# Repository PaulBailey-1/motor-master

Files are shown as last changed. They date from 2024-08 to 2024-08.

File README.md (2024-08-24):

# MotorMaster
This is a board designed to easily command FRC motors for testing or prototyping. It currently supports motors with the Talon FX motor controller. This repo contains the board schematics, PCB layout, and firmware for the board. 

## Features
It features 2 PWM channels that can be connected directly to the CAN connectors of the motor to command a duty cycle. Pressing the test button will output a 50% duty cycle on both PWM channels.  

The board can also be connected to motors through the CAN bus. Connect one end of the CAN chain to the CAN connector on the board and the other end to the TERM connector, or use another termination resistor. 
NOTE: CAN functionality is still experimental and may not work, feel free to work on it.

The e-stop button will prevent the board from outputting any commands until the MCU is reset with the reset button. 

The EXT pins can be used to connect an external input, like a switch or button, to provide additional control such as driving a motor or as an e-stop. The functionality must be added to the code, by default it does nothing.

The board can be powered through the USB C port, or from the power terminal off of a 12V battery. The board does not supply the motor with power, but it is important that it shares ground with the motor. 

The board is designed to be used over Bluetooth with its accompanying app, the source of which is here: https://github.com/PaulBailey-1/motor-master-app  
It is a cross-platform app and so should be able to be compiled for Android and iOS, but it has only been tested for Android. 

## Manufacturing
Board gerbers exported for manufacture by OSHPark are included in the repo, otherwise, the board can be opened in KiCad to export for manufacture. The BOM can be ordered from either Mouser or DigiKey.  

The FTDI header (J5) and the EXT header (J6) are optional. The USBC TVS diode (D2) may also be omitted since it is hard to solder without bridges, although it does make the USB lines vulnerable to damage from ESD. The USB C may also be omitted entirely (J1 & D2), and the board can be programmed through the FTDI header. 

To assemble the board, a stencil can be ordered and used to apply solder paste to the pads. The solder then may be reflowed in an oven or with hot air. It may also be possible to have it assembled by the PCB fab house.

## Programming
Dependencies:
* CAN by Sandeep Mistry v0.3.1
* ESP32Servo by Kevin Harrington & John K. Bennett v3.0.5

To program the board, connect to it with USB C or with an FTID adapter and program it with the Arduino IDE. Install the ESP32 boards and the required libraries, select 'ESP32S3 Dev Module' as the board, and upload.  

The name of the board over Bluetooth can have a postfix added to it in the code to help distinguish it.
The first time the board is programmed after being assembled, the Boot button must be held from when it is plugged until it has been flashed.
For debugging over USB C make sure the 'USB CDC On Boot' option is enabled so that you can get logging over the serial port.

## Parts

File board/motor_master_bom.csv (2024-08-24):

Reference | Value | Qty | Mfr_Number | Supplier | Supplier_Number
C1,C2,C4,C10 | 10uF | 4 | C0603C106M9PAC | Mouser | 80-C0603C106M9PAC
C3,C5,C6,C7,C8,C9,C11,C14 | 0.1uF | 8 | C0603C104K5RAC3121 | Mouser | 80-C603C104K5RAC3121
C12,C13 | 100p | 2 | C0603C101J1GAC7411 | Mouser | 80-C0603C101J1GACLR
C15 | 4.7n | 1 | C0603C472J5GACTU | Mouser | 80-C0603C472J5G
D1,D4 | SK14 | 2 | SK14 | Mouser | 637-SK14
D2 | TPD4E02B04DQAR | 1 | TPD4E02B04DQAR | Mouser | 595-TPD4E02B04DQAR
D3 | 150060RS75000 | 1 | 150060RS75000 | Mouser | 710-150060RS75000
D5 | 150060RS75000 | 1 | 150060VS75000 | Mouser | 710-150060VS75000
D6 | SZNUP2105LT1G | 1 | SZNUP2105LT1G | Mouser | 863-SZNUP2105LT1G
IC1 | LM1117MPX-3.3_NOPB | 1 | LM1117MPX-3.3/NOPB | Mouser | 926-LM1117MPX3.3NOPB
IC2 | SN65HVD232DR | 1 | SN65HVD232DR | Mouser | 595-SN65HVD232DR
J1 | USB4105-GF-A | 1 | USB4105-GF-A-120 | Mouser | 640-USB4105-GF-A-120
J2 | 5-12V | 1 | 1190297 | Mouser | 651-1190297
J3,J4,J7,J8 | -- mixed values -- | 4 | 705430002 | Mouser | 538-70543-0002
J5 | FTDI | 1 | M20-9990446 | Mouser | 855-M20-9990446
J6 | EXT | 1 | TSW-102-07-T-S | Mouser | 200-TSW10207TS
R1,R2 | 5.1k | 2 | CRCW06035K10FKEA | Mouser | 71-CRCW0603-5.1K-E3
R3,R9 | 100 | 2 | CRCW0603100RFKEA | Mouser | 71-CRCW0603-100-E3
R4,R5,R6,R7,R8 | 10k | 5 | CRCW060310K0FKEA | Mouser | 71-CRCW0603-10K-E3
R10,R11 | 60 | 2 | CRCW120660R0KNAIF | Mouser | 71-CRCW120660R0KNAIF
R12 | 120 | 1 | CRCW0603120RFKEA | Mouser | 71-CRCW0603-120-E3
S1,S2,S3 | -- mixed values -- | 3 | PTS636 SKG25J SMTR LFS | Mouser | 611-PTS636SKG25JSMTR
S4 | E-Stop | 1 | FSM4JH | Mouser | 506-FSM4JH
U1 | ESP32-S3-WROOM-1-N8 | 1 | ESP32-S3-WROOM-1-N8 | Mouser | 356-ESP32-S3WROOM1N8

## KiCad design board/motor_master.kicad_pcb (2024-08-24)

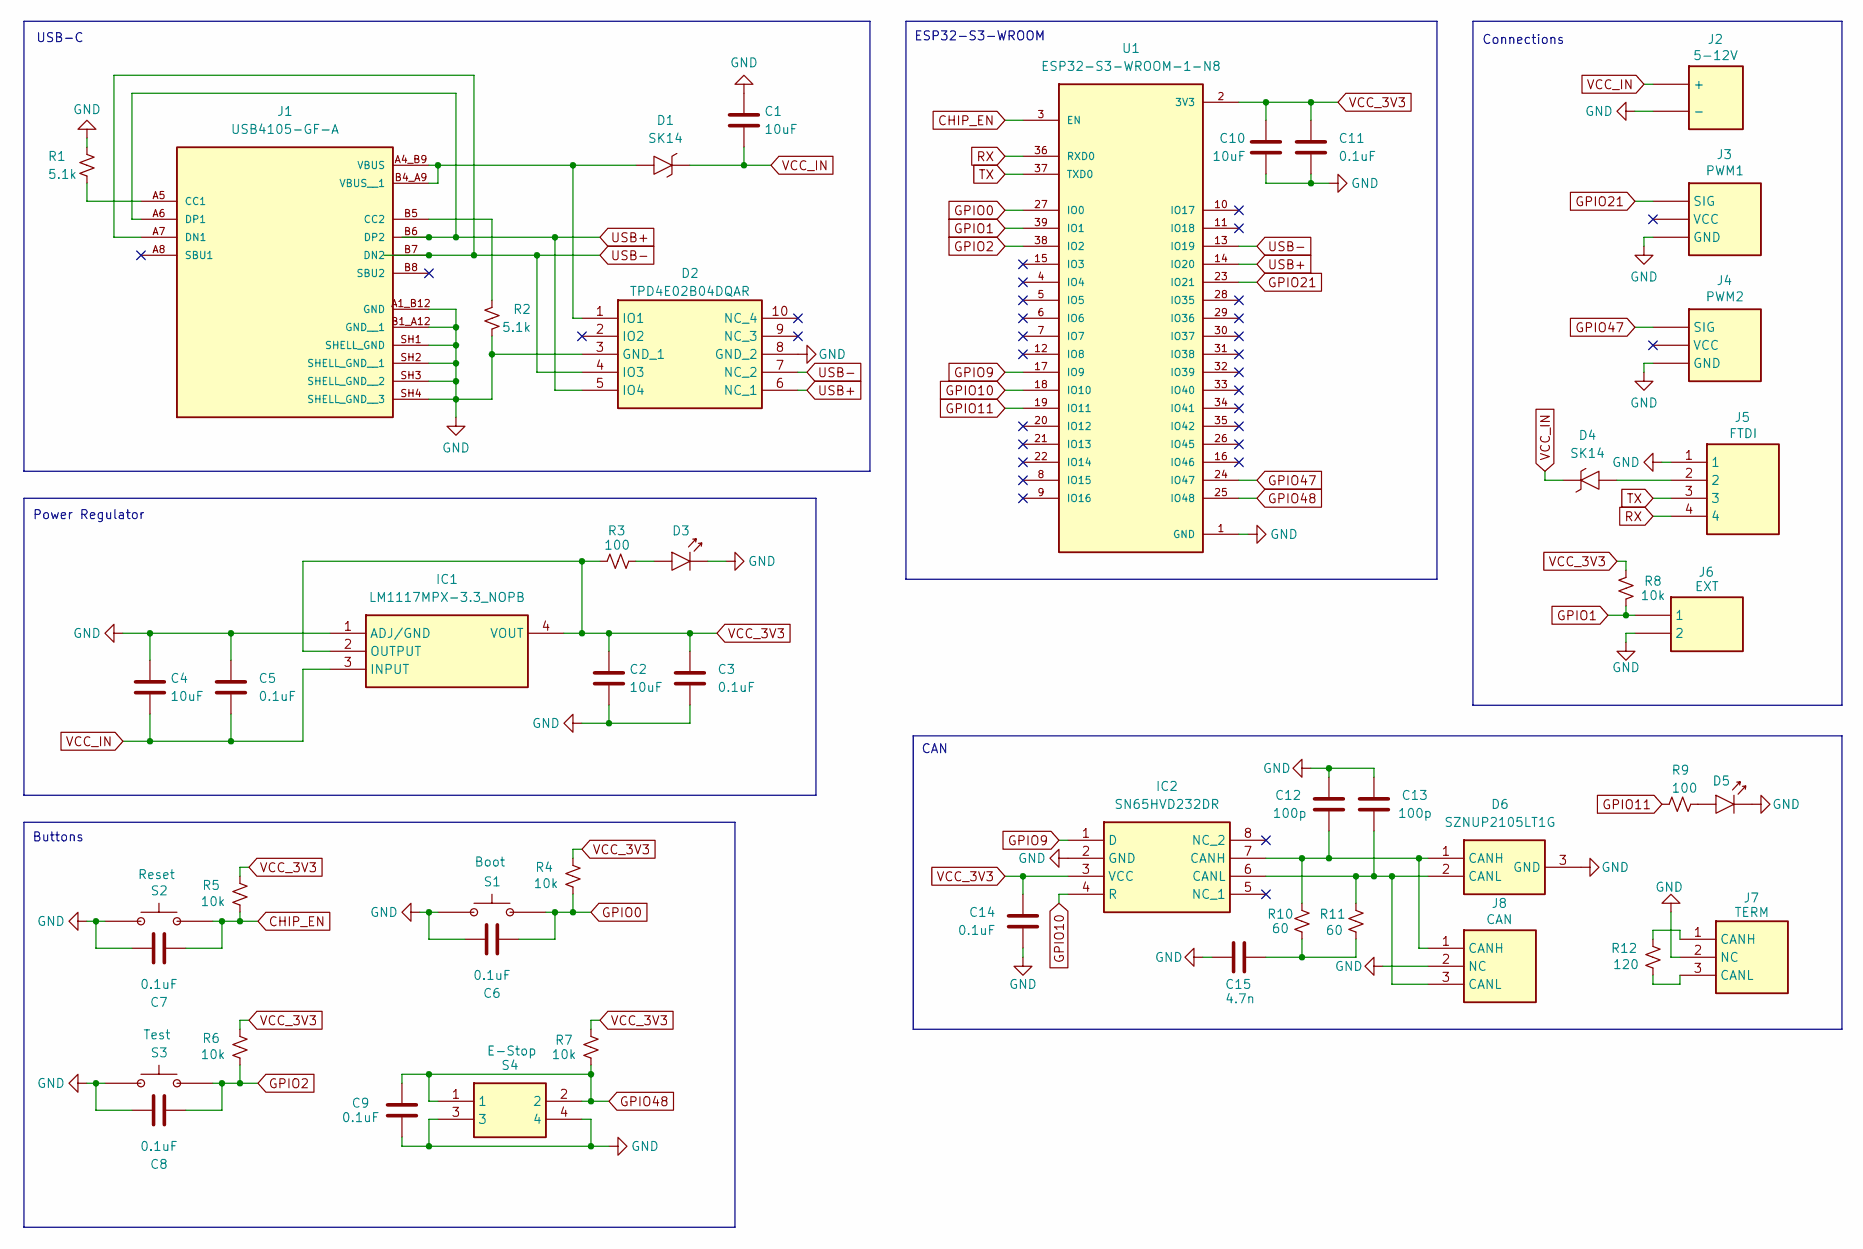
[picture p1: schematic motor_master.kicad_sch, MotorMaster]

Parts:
C1, C2, C4, C10: 10uF; C_0603_1608Metric
C3, C5, C6, C7, C8, C9, C11, C14: 0.1uF; C_0603_1608Metric
C12, C13: 100p; C_0603_1608Metric
C15: 4.7n; C_0603_1608Metric
D1, D4: SK14; DIONM5027X250N; Mouser Part Number 637-SK14
D2: TPD4E02B04DQAR; DQA_R-PUSON-N10_; Mouser Part Number 595-TPD4E02B04DQAR
D3, D5: 150060RS75000; LEDC1608X80N; Mouser Part Number 710-150060RS75000
D6: SZNUP2105LT1G; SOT96P237X111-3N; Mouser Part Number 863-SZNUP2105LT1G
IC1: LM1117MPX-3.3_NOPB; SOT230P700X180-4N; Mouser Part Number 926-LM1117MPX3.3NOPB
IC2: SN65HVD232DR; SOIC127P600X175-8N; Mouser Part Number 595-SN65HVD232DR
J1: USB4105-GF-A; GCT_USB4105-GF-A; PARTREV B3
J2: 5-12V; 1190297; Mouser Part Number 651-1190297
J3: PWM1; 1719710103; Mouser Part Number 200-TSW10307TS
J4: PWM2; 1719710103; Mouser Part Number 200-TSW10307TS
J5: FTDI; HDRV4W64P0X254_1X4_1016X254X889P; Mouser Part Number 855-M20-9990446
J6: EXT; TSW-102-XX-YY-S; Mouser Part Number 200-TSW10207TS
J7: TERM; 1719710103; Mouser Part Number 200-SSW10301FS
J8: CAN; 1719710103; Mouser Part Number 200-TSW10307TS
R1, R2: 5.1k; R_0603_1608Metric
R3, R9: 100; R_0603_1608Metric
R4, R5, R6, R7, R8: 10k; R_0603_1608Metric
R10, R11: 60; R_1206_3216Metric
R12: 120; R_0603_1608Metric
S1: Boot; PTS636SKG25JSMTRLFS; Mouser Part Number 611-PTS636SKG25JSMTR
S2: Reset; PTS636SKG25JSMTRLFS; Mouser Part Number 611-PTS636SKG25JSMTR
S3: Test; PTS636SKG25JSMTRLFS; Mouser Part Number 611-PTS636SKG25JSMTR
S4: E-Stop; FSM4JH; Mouser Part Number 506-FSM4JH
U1: ESP32-S3-WROOM-1-N8; XCVR_ESP32-S3-WROOM-1-N8

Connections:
CHIP_EN: C7.2, R5.1, S2.2 (NO), U1.3 (EN)
GND: C1.1, C2.2, C3.2, C4.1, C5.1, C6.1, C7.1, C8.1, C9.2, C10.2, C11.2, C12.2, C13.2, C14.1, C15.1, D2.3 (GND_1), D2.8 (GND_2), D3.2 (A), D5.2 (A), D6.3 (GND), IC1.1 (ADJ/GND), IC2.2 (GND), J1.A1_B12 (GND), J1.B1_A12 (GND__1), J1.SH1 (SHELL_GND), J1.SH2 (SHELL_GND__1), J1.SH3 (SHELL_GND__2), J1.SH4 (SHELL_GND__3), J2.3 (-), J2.4 (-), J3.3 (GND), J4.3 (GND), J5.1, J6.2, J7.2 (NC), J8.2 (NC), R1.1, R2.2, S1.1 (COM), S2.1 (COM), S3.1 (COM), S4.3, S4.4, U1.1 (GND), U1.40 (GND), U1.41_1 (GND), U1.41_2 (GND), U1.41_3 (GND), U1.41_4 (GND), U1.41_5 (GND), U1.41_6 (GND), U1.41_7 (GND), U1.41_8 (GND), U1.41_9 (GND)
GPIO0: C6.2, R4.1, S1.2 (NO), U1.27 (IO0)
GPIO1: J6.1, R8.1, U1.39 (IO1)
GPIO2: C8.2, R6.1, S3.2 (NO), U1.38 (IO2)
GPIO9: IC2.1 (D), U1.17 (IO9)
GPIO10: IC2.4 (R), U1.18 (IO10)
GPIO11: R9.2, U1.19 (IO11)
GPIO21: J3.1 (SIG), U1.23 (IO21)
GPIO47: J4.1 (SIG), U1.24 (IO47)
GPIO48: C9.1, R7.1, S4.1, S4.2, U1.25 (IO48)
unnamed: C15.2, R10.1, R11.1
unnamed: D1.2 (A), D2.1 (IO1), J1.A4_B9 (VBUS), J1.B4_A9 (VBUS__1)
unnamed: D3.1 (K), R3.1
unnamed: D4.2 (A), J5.2
unnamed: D5.1 (K), R9.1
unnamed: C12.1, D6.1 (CANH), IC2.7 (CANH), J8.1 (CANH), R10.2
unnamed: C13.1, D6.2 (CANL), IC2.6 (CANL), J8.3 (CANL), R11.2
unnamed: J1.A5 (CC1), R1.2
unnamed: J1.B5 (CC2), R2.1
unnamed: J7.1 (CANH), R12.2
unnamed: J7.3 (CANL), R12.1
RX: J5.4, U1.36 (RXD0)
TX: J5.3, U1.37 (TXD0)
USB+: D2.5 (IO4), D2.6 (NC_1), J1.A6 (DP1), J1.B6 (DP2), U1.14 (IO20)
USB-: D2.4 (IO3), D2.7 (NC_2), J1.A7 (DN1), J1.B7 (DN2), U1.13 (IO19)
VCC_3V3: C2.1, C3.1, C10.1, C11.1, C14.2, IC1.2 (OUTPUT), IC1.4 (VOUT), IC2.3 (VCC), R3.2, R4.2, R5.2, R6.2, R7.2, R8.2, U1.2 (3V3)
VCC_IN: C1.2, C4.2, C5.2, D1.1 (K), D4.1 (K), IC1.3 (INPUT), J2.1 (+), J2.2 (+)

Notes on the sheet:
USB-C
Connections
ESP32-S3-WROOM
CAN
Power Regulator
Buttons

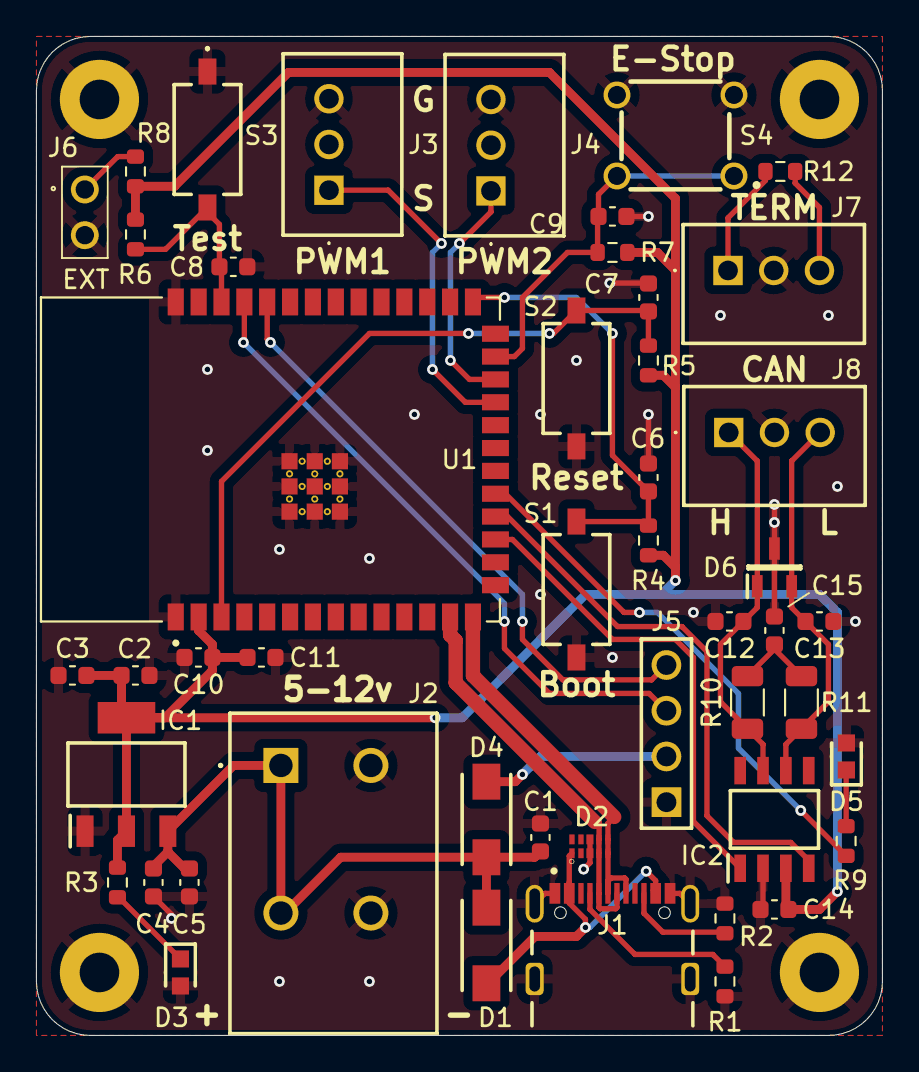
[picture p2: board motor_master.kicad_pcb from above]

Board: 2 copper layers, 47.0 x 55.5 mm, 48 parts (0 on the bottom side), 28 nets.

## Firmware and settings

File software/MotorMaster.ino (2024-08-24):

#include <map>
#include <ESP32Servo.h>

#include "BluetoothServer.h"
#include "CanConnection.h"
#include "CanMotorController.h"

// Add a postfix to distingish the device
String namePostfix = "";

// See the following for generating UUIDs:
// https://www.uuidgenerator.net/

#define SERVICE_UUID "4f79cca2-cef2-4137-b4f1-c9cc7fda9ec7"
#define PWM1_ENABLE_CHARACTERISTIC_UUID "a506df5a-48b5-4f57-933c-214612bd77ef"
#define PWM1_CMD_CHARACTERISTIC_UUID "ead5e8a1-e5ea-4223-86e5-7ff501a37929"
#define PWM2_ENABLE_CHARACTERISTIC_UUID "1c9eb4ba-a11f-444b-aeca-0765f9387506"
#define PWM2_CMD_CHARACTERISTIC_UUID "c8bd31cf-6364-4aab-8949-d55cca13618f"
#define CAN_ENABLE_CHARACTERISTIC_UUID "73bb062a-be94-4a95-8fd0-8460d7a8af88"
#define CAN_INFO_CHARACTERISTIC_UUID "77723d0f-9668-466e-a3f2-56bc80a0eb9d"
#define CAN_CMD_CHARACTERISTIC_UUID "28332f90-0151-479a-8bab-f627c195533c"

const int PWM_OUTPUT_1_PIN = 21;
const int PWM_OUTPUT_2_PIN = 47;
const int CAN_TX_PIN = 9;
const int CAN_RX_PIN = 10;
const int CAN_LED_PIN = 11;
const int TEST_BTN_PIN = 2;
const int ESTOP_BTN_PIN = 48;
const int EXTERN_PIN = 1;

int testDC = 50;
bool estopped = false;

BluetoothServer* btServer;

Servo pwm1Servo;
Servo pwm2Servo;

bool pwm1Enabled = false;
int pwm1UserCmd = 50; // percent DC
int pwm1Cmd = 0;

bool pwm2Enabled = false;
int pwm2UserCmd = 50;
int pwm2Cmd = 0;

bool canEnabled = false;
char canInfo[256] = "";
CanMotorCmd canCmd = {-1, 0.0};
std::map<int, CanMotorController*> canDevices;

void queryCanDevices() {
    delay(300);

    for (auto i = canDevices.begin(); i != canDevices.end(); i++) {
        delete i->second;
    }
    
    // Dummy code
    canDevices[1] = new TalonFX(1);
    const char* info = "[ { \"id\": 1, \"name\": \"drive_motor\" } ]";
    strcpy(canInfo, info);
}

void sendHeartBeat() {
    twai_message_t message = {
        .identifier = 0x01011840,
        .data_length_code = 8,
        .data = {0},
    };
    message.data[4] = 0b00001000;
    if (canEnabled) message.data[4] |= 0b01000000;
    canSend(message);
}

void setup() {
    Serial.begin(115200);
    Serial.println("Starting MotorMaster");

    btServer = new BluetoothServer("MotorMaster" + namePostfix, SERVICE_UUID);
    btServer->bindCharacteristic(pwm1Enabled, PWM1_ENABLE_CHARACTERISTIC_UUID);
    btServer->bindCharacteristic(pwm1UserCmd, PWM1_CMD_CHARACTERISTIC_UUID);
    btServer->bindCharacteristic(pwm2Enabled, PWM2_ENABLE_CHARACTERISTIC_UUID);
    btServer->bindCharacteristic(pwm2UserCmd, PWM2_CMD_CHARACTERISTIC_UUID);
    btServer->bindCharacteristic(canEnabled, CAN_ENABLE_CHARACTERISTIC_UUID);
    btServer->bindCharacteristic(canInfo, CAN_INFO_CHARACTERISTIC_UUID, queryCanDevices);
    btServer->bindCharacteristic(canCmd, CAN_CMD_CHARACTERISTIC_UUID);
    btServer->start();

    canStart(CAN_TX_PIN, CAN_RX_PIN);

    pinMode(CAN_LED_PIN, OUTPUT);
    pinMode(TEST_BTN_PIN, INPUT);
    pinMode(ESTOP_BTN_PIN, INPUT);
    // pinMode(EXTERN_PIN, INPUT);

    Serial.println("Started");

}

void loop() {

    // Read BT bound params
    btServer->bindMutex.lock();
    if (pwm1Enabled) {
        pwm1Cmd = pwm1UserCmd;
    } else {
        pwm1Cmd = 0;
    }
    if (pwm2Enabled) {
        pwm2Cmd = pwm2UserCmd;
    } else {
        pwm2Cmd = 0;
    }
    if (canCmd.id != -1) {
        if (canDevices.find(canCmd.id) == canDevices.end()) {
            Serial.printf("ERROR: Failed cmd nonexistant CAN device %i\n", canCmd.id);
        } else {
            canDevices[canCmd.id]->cmd = canCmd;
        }
        canCmd.id = -1;
    }
    btServer->bindMutex.unlock();
    sendHeartBeat();

    // Handle buttons
    bool testBtn = !digitalRead(TEST_BTN_PIN);
    if (testBtn) {
        pwm1Cmd = testDC;
        pwm2Cmd = testDC;
    }
    if (!digitalRead(ESTOP_BTN_PIN)) {
        estopped = true;
        Serial.println("e-stopped");
    }

    // Handle CAN
    digitalWrite(CAN_LED_PIN, canRecieve());
    getCanAlerts();
    // getCanStatus();

    if (estopped) {
        pwm1Enabled = false;
        pwm2Enabled = false;
        testBtn = false;
        canEnabled = false;
    }

    // Command outputs
    // Hopefully, because the bound bools are only being read, this doesn't need to be locked
    if (pwm1Servo.attached()) pwm1Servo.write(map(pwm1Cmd, -100, 100, 1, 179));
    if (!pwm1Enabled && !testBtn && pwm1Servo.attached()) pwm1Servo.detach();
    if ((pwm1Enabled || testBtn) && !pwm1Servo.attached()) pwm1Servo.attach(PWM_OUTPUT_1_PIN);

    if (pwm2Servo.attached()) pwm2Servo.write(map(pwm2Cmd, -100, 100, 1, 179));
    if (!pwm2Enabled && !testBtn && pwm2Servo.attached()) pwm2Servo.detach();
    if (pwm2Enabled || testBtn && !pwm2Servo.attached()) pwm2Servo.attach(PWM_OUTPUT_2_PIN);

    if (canEnabled) {
        for (auto i = canDevices.begin(); i != canDevices.end(); i++) {
            i->second->command();
        }
    }

    delay(20);
}

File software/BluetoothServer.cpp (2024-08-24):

#include <functional>

#include "BluetoothServer.h"

BindCharacteristicCallback::BindCharacteristicCallback(uint8_t* var, size_t len, std::mutex* mutex) : BLECharacteristicCallbacks() {
    _var = var;
    _len = len;
    _mutex = mutex;
}

BindCharacteristicCallback::BindCharacteristicCallback(uint8_t* var, size_t len, std::mutex* mutex, std::function<void()> onReadCallback)
    : BindCharacteristicCallback(var, len, mutex) {
    _onReadCallback = onReadCallback;
}

void BindCharacteristicCallback::onWrite(BLECharacteristic* characteristic, esp_ble_gatts_cb_param_t* param) {
    if (param->write.len > _len) {
        Serial.println("Error: incoming data is to long");
    } else {
        _mutex->lock();
        memcpy(_var, param->write.value, param->write.len);
        _mutex->unlock();
        Serial.println("Data written for " + characteristic->getUUID().toString());
        // Serial.prinf("(%i bytes) ", param->write.len);
        // for (int i = 0; i < param->write.len; i++) {
        //     Serial.printf("%02X ", param->write.value[i]);
        // }
        // Serial.println();
    }
}

void BindCharacteristicCallback::onRead(BLECharacteristic* characteristic, esp_ble_gatts_cb_param_t* param) {
    if (_onReadCallback) _onReadCallback();
    characteristic->setValue(_var, _len);
}


void ServerCallbacks::onConnect(BLEServer* pServer) {
    Serial.println("Client Connected");
};

void ServerCallbacks::onDisconnect(BLEServer* pServer) {
    Serial.println("Client Disconnected");
    BLEDevice::startAdvertising();
}

BluetoothServer::BluetoothServer(String name, String service_UUID) {

    Serial.printf("Starting Bluetooth server for %s\n", name.c_str());
    BLEDevice::init(name);
    _server = BLEDevice::createServer();
    _server->setCallbacks(new ServerCallbacks());
    _service = _server->createService(service_UUID);
    _service_UUID = service_UUID;
}

void BluetoothServer::start() {
    _service->start();
    BLEAdvertising* advertising = BLEDevice::getAdvertising();
    advertising->addServiceUUID(_service_UUID);
    advertising->setScanResponse(true);
    advertising->setMinPreferred(0x06);  // functions that help with iPhone connections issue
    advertising->setMinPreferred(0x12);
    BLEDevice::startAdvertising();
}

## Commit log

2024-07-22 Board revisions from design review
    [motor_master.kicad_pcb, motor_master.kicad_sch, motor_master_bom.csv]
2024-07-23 Changed power diodes
    [motor_master.kicad_pcb, motor_master.kicad_sch, motor_master_bom.csv]
2024-07-26 Updated BOM with manufactuer numbers
    [motor_master.kicad_pcb, motor_master.kicad_sch, motor_master_bom.csv]
2024-07-26 Added gerber
2024-08-19 Changed LEDs and fixed estop button wiring
    [motor_master.kicad_pcb, motor_master.kicad_sch, motor_master_bom.csv]
2024-08-24 Added pullup resistor to extern pin, renumbered parts
    [motor_master.kicad_pcb, motor_master.kicad_sch, motor_master_bom.csv]
2024-08-24 Added some framework for can, fixed some other bugs
    [BluetoothServer.cpp, MotorMaster.ino]
